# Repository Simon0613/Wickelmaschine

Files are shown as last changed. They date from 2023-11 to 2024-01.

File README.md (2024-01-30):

# Wickelmaschine

### Die Entwicklung und Konstruktion, sowie die Herstellung des Prototyps erfolgte im Rahnen einer Masterarbeit an der Hochschule Osnabrück.

Mit dieser Wickelmaschine können faserverstärkte Rohre z.B. (CFK o. GFK) hergestellt werden. Die Abmessungen der Rohre können nach individuellen Wünschen gestaltet werden und können u.a. für Sport und Campingequipment verwendet werden. Die Maschine arbeitet nach dem Tapelege- oder Tapewickelverfahren, bei dem unidirektional verstärkte Kunststofftapes um den Kern gewickelt und durch eine Wärmequelle mit den unteren Schichten verbunden werden.

Wickelmaschine

Die Wickelmaschine kann mit einfachen Fertigungsverfahren hergestellt werden. Der größte Teil der Bauteile kann mit einem FDM-3D-Drucker angefertigt werden. Weiterhin werden Normteile wie Schrauben, Lager, Einschmelzmuttern und Federn verwendet. Für den Antrieb der Achsen werden Komponenten verwendet die sich in vielen 3D-Druckern wiederfinden: Schrittmotoren, GT2- Riemen und Riemenscheiben, Arduino Uno, CNC-Shield usw.  Der Rest besteht aus Halbzeugen wie Rohren und Flachprofile, die zugesägt, gebohrt und ein wenig gefeilt werden müssen. 

Prototyp

Die Dimensionen der Rohre können nach persönlichen Anforderungen gestalltet werden. Die Maschine kann Rohre mit einen Durchmesser von 15-55 mm herstellen. Die Länge der Rohre ist beliebig einstellbar, nur die Wickelmaschine muss im vorhinein auf die gewünschten Rohrlängen passend angefertigt sein.

3RohreUnterschiedliche Teilung
Nahaufnahme
Überblick Rohre

LizenzOSH

# Montageanleitung

### Folgendes Werkzeug wird für den Bau der Anlage benötigt:

- Bohrmaschine
- Werkzeug zum Anzeichnen der Bohrungen
- Flachfeile
- 3,3 mm Bohrer
- 4,5 mm Bohrer
- M4 Gewindeschneider
- Kegelsenker
- Stirnsenker für M4 Zylinderschrauben
- Lötkolben
- Maßband
- Säge
- Reiniger
- Innensechskantschlüsselsatz

### Aufbauanleitung
Nachdem alle Bauteile entsprechend der Stückliste besorgt wurden, kann mit dem Bauteilzuschnitt begonnen werden. Dazu werden die Rohre entsprechend der Zeichnung_Wellenzuschnitt abgelängt. Die Rohre mit der Bezeichnung T005_Führungsrohr und T060_Kern können je nach persönlichem Wunsch auf eine individuelle Länge abgelängt werden. Sollte der Wunsch bestehen eine Anlage für längere Rohre zu bauen. Die Wellen und Achsen können ebenfalls nach der Zeichnung_Wellenzuschnitt abgelängt werden. Es wird empfohlen die Rohr- und Wellenenden zu entgraten, um sie später besser montieren zu können.
Die Bauteile, die gedruckt werden müssen, sind in folgender Tabelle mit der benötigten Stückzahl gekennzeichnet. Zusätzlich können der Tabelle die Druckeinstellungen für die 3D-Druckteile entnommen werden. Einige Bauteile sind mit „Optional“ markiert, die nur gedruckt werden müssen, sobald ein Material oder eine andere Düse verwendet wird.

1. Zusammenbau der Baugruppe B02_Tapeklemme.
2. 2-mal Zusammenbau Baugruppe B03_Führungswagen.
3. Zusammenbau Baugruppe B05_Grundaufbau_links.
4. Die Baugruppen B03_Führungswagen werden auf die beiden Rohre T005_Führungsrohr aufgeschoben.
5. Die Baugruppen B03_Führungswagen werden mit dem Bauteil T022_Grundplatten mit 12 Innensechskantschrauben verschraubt.
6. Die Baugruppe B06_Grundaufbau_rechts montieren. Hierbei werden die zwei Bauteile T02_Tapeklemme nur leicht eingeschraubt.
7. Die Baugruppe B06_Grundaufbau_rechts wird an die Baugruppe B05_Grundaufbau_links montiert. Jetzt können auch die zwei Klemmen T02_Tapeklemme fest angezogen werden.
8. Die Baugruppe B04_Lagerung_links zusammenbauen. Dazu werden die beiden Klemmen T03_Klemme2 leicht an die Rohre T004_Verbindungsrohr geschraubt. Hier sollte der Abstand von 16,4 mm zwischen dem T019_Riemenspannerhalter und T07_Lagerung_links beachtet werden. Ebenfalls muss auf die Position der beiden Baugruppe relativ zu dem Bauteil T01_Standfuß geachtet werden, die Positionen sind in der Zeichnung B01_Wickelanlage eingezeichnet.
9. Bevor die Baugruppe B07_Antrieb_Rotation an die Rohre T004_Verbindungsrohr angebracht wird, müssen erst folgende Bauteile zusammengefügt werden. Die Riemenscheibe N_Riemenscheibe_GT2_60Z_D8 wird zusammen mit dem N_Riemen_320 auf die Welle T013_Antriebswelle aufgeschoben, der benötigte Abstand ist in der Zeichnung B07_Antrieb_Rotation angegeben. Anschließend wird die Welle T013_Antriebswelle zwischen den Bauteilen T011_Lagergehäuse und T012_Lagergehäuse eingeklemmt. Dieser Verbund wird nun an das Bauteil T09_Lagerung_rechts angeschraubt. Anschließend wird der N_Schrittmotor_Nema17 an T010_Motorbefestigung angeschraubt. Die Riemenscheibe N_Riemenscheibe_GT2_20Z_D5 wird erst auf die Schrittmotorwelle geschoben, nachdem die T010_Motorbefestigung in die Führung von der
T09_Lagerungrechts eingeführt worden ist. Die Spannung der T010_Motorbefestigung und das endgültige Anziehen der T018_Riemenklemme erfolgt später. Die Position der Baugruppe B07_Antrieb_Rotation auf den Rohren T004_Verbindungsrohr ist in Zeichnung B01_Wickelanlage angegeben.
10. Die Montage der Baugruppe B08_Verfahreinheit kann bereits vor dem Schritt 4 ausgeführt werden. Innerhalb der Baugruppe B08_Verfahreinheit wird zuerst die Baugruppe B11_Schwenktisch zusammengebaut. Zuerst müssen die N_Rillenkugellager DIN 625 6000 2Z auf die T029_Achse aufgeschoben werden, die Bemaßung ist in der Schnittansicht der Zeichnung B11_Schwenktisch angegeben. Anschließend werden die beiden Lagerhälften T030_Lager und T030_Lager_Gegenstück zusammen mit T029_Achse verschraubt. Das Bauteil T031_Hülse kann auf die T029_Achse gesetzt werden. Die Bauteile N_Riemenscheibe GT2 60Z D10 und T028_Schwenkplatte werden erst in der Baugruppe B08_Verfahreinheit montiert. Dazu wird der N_Riemen_200 auf die Riemenscheibe N_Riemenscheibe GT2 60Z D10 gelegt und mit der T028_Grundplatte verschraubt. Anschließend kann die Madenschraube der N_Riemenscheibe GT2 60Z D10 angezogen werden, nachdem diese auf die T029_Achse geschoben ist. Im Anschluss können die beiden Schrittmotoren nach der Zeichnung B08_Verfahreinheit an die Bauteile T014_Motorbefestigung2 und T032_Motorbefestigung3 angeschraubt werden. Zuletzt müssen diese an die T022_Grundplatte montiert werden.
11. Die Baugruppe B09_Materialspeicher montieren. Die Feder N_Druckfeder DIN2098 1x10x30 kann je nach Wunsch, stärker gespannt werden, indem die N_Stellring 5mm näher Richtung T037_Materialspeicher geschoben werden.
12. Der Heißluftföhn wird zwischen die Bauteile T046_HalterO und T046_HalterU geklemmt. Diese Baugruppe kann auch auf die T028_Schwenkplatte geschraubt werden. Über die Langlöcher kann die horizontale Entfernung zu dem Kern eingestellt werden. Durch Benutzung der Distanzscheiben T058_Distanzstück wird die vertikale Position zum Kern eingestellt.
13. Die Baugruppe B10_Andrückrolle nach vorliegender Zeichnung montieren. Das Bauteil T057_Tapeführung ist in mehreren Ausführungen vorhanden. Diese sind abhängig von der verwendeten Tapebreite und kann dementsprechende gewechselt werden.
14. Die Baugruppe B02_Tapeklemme auf das Bauteil T060_Kern aufschieben. Anschließend den T060_Kern an der Antriebsseite anschrauben und an der gegenüberliegenden Seite mit zwei T042_Zentrierteil fixieren.
15. Der Heißluftföhn sowie die Baugruppe B09_Materialspeicher können jetzt auf der T028_Schwenkplatte montiert werden.
16. Für die Montage der B10_Andrückrolle ist es empfehlenswert, dass Bauteil T033_Federung durch Lösen von vier Schrauben zu demontieren. Die B10_Andrückrolle auf der T028_Schwenkplatte zu montieren. Anschließend dann das Bauteil T033_Federung wieder anschrauben.
17. Der mechanische Teil der Wickelanlage ist jetzt fertig. Nun folgt der elektrische Teil.

## Elektronik und Steuerung

18. Das CNC-Shield auf den Arduino UNO stecken.
19. Die Jumper auf die für die Treiber vorgesehenen Plätze gemäß der Anleitung des CNC-Shields auf 1/8 Schritte stecken.

JumperPositionierung

20. Die A4988 Schrittmotortreiber auf die X-, Y- und Z-Position aufstecken. Hier ist unbedingt auf die richtige Orientierung zu Achten.
21. Danach werden die Schrittmotorkabel an den Motor sowie an das CNC-Shield angeschlossen. Die X-, Y- und Z-Anschlüsse sind auf dem CNC-Shield und auf folgender Abbildung angezeichnet

MotorBezeichnung

22. Den Arduino UNO mit Strom versorgen und das USB-B Kabel an einen Computer anschließen.

# Estlcam
1. Estlcam auf einem Computer installieren.
2. Anschließend können folgende Einstellungen übernommen werden. Unter dem Menü Einstellungen müssen bei CNC-Steuerung, Grundeinstellungen und CNC Programme Einstellungen vorgenommen werden.
3. Grundeinstellungen und CNC Programme 

GrundeinstellungenESTLCAM

4. CNC Steuerung: Die abgebildeten Werte können einfach übernommen werden. Nachdem alle Werte eingetragen sind sollten diese auch gespeichert werden. Danach kann auf die Schaltfläche Steuerung programmieren geklickt werden.
CNC Steuerung

## Programmabfolge eingeben

1. Die Programmierung der Rohrewicklungen erfolgt über die G-Codes, ähnlich zu einer CNC-Steuerung. Hier muss nur etwas umgedacht werden:

Der Winkel der gewickelt werden soll ergibt sich aus der Bewegung in X-Richtung und der Anzahl der Umdrehungen des Kerns

X-Achse: Die X-Achse entspricht der Länge des Rohres. Dementsprechend wird für ein 100 mm  langes Rohr die Eingabe 100 getätigt.

Z-Achse: Die Z-Achse gibt die Anzahl der Drehungen eines Rohrs vor. Der Kern führt eine Umdrehung(360°) bei einer Eingabe von 100 aus.

Y-Achse: Die Y-Achse passt sich an der Wickelwinkel an. Bei einem Winkel von 45° wird die Y-Achse auf den Wert 4,5 eingestellt.
Achtung! Der Wickelwinkel wird immer von dem Kern gemessen! Das bedeutet wird das Tape gerade um den Kern gewickelt beträgt der Wickelwinkel 90°. Bei der Eingabe muss aber 0 eingegeben werden. Ähnlich bei einem Wickelwinkel von 80° Die Eingabe beträgt hier 1 Bei 70°->2, 60°->3, 50°->4, 45°->4,5

Der maximale Wickelwinkel beträgt 45°. Eingaben der Y-Achse die größer 4,5 sind führen zu einer Kollision.

Grundsätzlich gibt es zwei Arten von Wicklungen einmal Kreuzwickeln und Umfangswickeln

Umfangswickeln: Hier wird während einer Schicht das Tape direkt an das nächste gelegt. Somit wird eine Schicht bei einer Verfahrbewegung fertig.
Diese Art eignet sich besonders wenn Rohre benötigt werden die mit einem Druck von Innen stehen. Beispielhaft wie ein Schlauch oder Tank.

Kreuzwickeln: Diese Wicklungsart ist ein wenig aufwändiger, hat aber dafür vielfältigere Einsatzmöglichkeiten. Diese Rohre eignen sich hervorragend für torsionsbelastete Rohre wie beispielweise Antriebswellen.
Hierbei wird eine Schicht erst durch mehrmaliges hin und zurückfahren fertiggestellt. Die Wicklungen werden dabei kreuzweise übereinandergelegt.

Vor Beginn muss überlegt werden wie viele Umwicklungen man auf einer Rohrlänge haben möchte. Dazu wird der Ausßenradius des Kerns benötigt. Anschließend kann mit folgenden Formel der Wickelwinkel ausgerechnet werden:

FormelnWickelwinkel

Als Beispiel wird dies an einem Rohr mit einer Länge von 100 mm gezeigt das nach dem Umfangswickelprinzip gewickelt wird.

Erstellung Programmabfolge

Die Programme können einfach im Text Editor erstellt werden. Bei Fertigstellung des Programms wird der Dateityp von .txt in . nc geändert. Danach kann ESTLCAM das Programm einlesen.

Die Wicklung der Rohre erfolgt in folgender Reihenfolge. Grundsätzlich kann sich an die folgende Vorgehensweise gehalten werden:

grafik
Im ersten Schritt werden vorbereitende Maßnahmen durchgeführt. Dazu gehört den Kern reinigen und das Material auf den B09_Materialspeicher aufzuwickeln. Die Position der Y-Achse wird ausgerichtet, indem T022_Grundplatte und T028_Schwenkplatte parallel zueinander ausgerichtet werden. Die Z-Achse kann auf 0 gesetzt werden. Die X-Achse kann an gewünschter Position auf 0 gesetzt werden, jedoch sollte auf die ausreichende Länge geachtet werden.
Anschließend wird das Material über die T050_Umlenkrolle gelegt und durch die T039_Materialzuführ geführt. Danach wird das Material unter die Andrückrolle geführt und min. zweimal um den Kern gewickelt. Das Ende wird durch die B02_Tapeklemme festgeklemmt. Jetzt kann das Programm in Estlcam hochgela-den werden. Zuerst wird der Heißluftföhn eingeschaltet und für ca. 30 s angelas-sen. Nachdem die Vorheizzeit vorüber ist, wird das Programm gestartet. Wenn das Programm durchgelaufen ist, kann der Heißluftföhn ausgeschaltet werden und das Material wird direkt am Kern durchtrennt. Sobald der Kern abgekühlt ist, kann die-ser aus der Anlage entfernt werden. Danach kann das fertige Rohr vom Kern ab-gezogen werden.

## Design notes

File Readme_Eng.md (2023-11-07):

# Windingmachine

### This winding machine was developed and built as part of a master's thesis at the University of Applied Sciences in Osnabrück, Germany.  

This winding machine can be used to produce fibre reinforced tubes. The dimensions of the tubes can be customised for use in sports and camping equipment, for example. The machine uses the tape laying or tape winding process, where unidirectional reinforced plastic tapes are wound around the core and bonded to the lower layers using a heat source.

Wickelmaschine

The winding machine can be produced using simple manufacturing methods. Most of the components can be produced using an FDM 3D printer. Standard parts such as bolts, screws, bearings, heat sink inserts and springs are used. The power unit includes stepper motors and other parts you can find in 3D printers, such as GT2 pulleys and belts, the Arduino uno and a CNC shield. The other components are semi-finished materials, such as tubes and profiles, which need to be machined with drills, saws and files.

Prototyp
The dimensions of the tubes can be customised. The machine is capable of producing tubes ranging from 15-55 mm ( 0.6 - 2.1 inches). The lengths of the tubes can be adjusted as required, but the winding machine must be built long enough.
3RohreUnterschiedliche Teilung
Nahaufnahme
Überblick Rohre

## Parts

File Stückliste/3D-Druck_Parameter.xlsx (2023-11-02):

 |  |  |  | Material
Name | Fülldichte | Wandstärke | Anzahl | PLA/PETG | ABS/ASA | PA
T001_Standfuß | 20% | 5 | 2 | xxx | xxx | x
T001_Standfuß_gsp | 20% | 5 | 2 | xxx | xxx | x
T002_Klemme1 | 20% | 5 | 4 | xxx | xxx | x
T003_Klemme2 | 20% | 5 | 7 | xxx | xxx | x
T006_Führungswagen | 20% | 5 | 2 | xxx | xxx | x
T007_Lagerung_links | 20% | 5 | 1 | xxx | xxx | x
T008_Lagerungshalter | 20% | 5 | 1 | xxx | xxx | x
T009_Lagerung_rechts | 20% | 5 | 1 | xxx | xxx | x
T010_Motorbefestigung | 20% | 5 | 1 | xxx | xxx | x
T011_Lagergehäuse | 20% | 4 | 1 | xxx | xxx | x
T012_Lagergehäuse | 20% | 4 | 1 | xxx | xxx | x
T014_Motorbefestigung2 | 20% | 4 | 1 | xxx | xxx | x
T015_Halter | 20% | 4 | 1 | xxx | xxx | x
T016_Klemme Riemen | 20% | 3 | 1 | xxx | xxx | x
T017_Riemenklemme | 20% | 3 | 1 | xxx | xxx | x
T018_Riemenspanner_H | 20% | 4 | 1 | xxx | xxx | x
T019_RiemenspannerHalter | 20% | 4 | 1 | xxx | xxx | x
T020_RiemenspannerHalter2 | 20% | 4 | 1 | xxx | xxx | x
T023_Materialhalter | 15% | 3 | 1 | xxx | xxx | x
T024_Klemmhebel | 20% | 3 | 1 | - | xx | xxx
T025_Tapeklemme | 20% | 4 | 1 | - | xxx | xxx
T026_Spule | 20% | 4 | 1 | xxx | xxx | x
T030_Lager | 40% | 5 | 1 | xx | xxx | xx
T030_Lager_Gegenstück | 40% | 5 | 1 | xx | xxx | xx
T031_Hülse | 20% | 4 | 1 | xx | xxx | xx
T032_Motorbefestigung3 | 20% | 4 | 1 | xxx | xxx | x
T033_Federung | 20% | 4 | 1 | x | xxx | xxx
T034_Federhalter | 20% | 5 | 1 | x | xxx | xxx
T035_Schieber | 30% | 5 | 1 | - | xx | xxx
T037_Materialspeicher | 20% | 3 | 1 | xxx | xxx | x
T037_Materialspeicher_Gegenstück | 20% | 3 | 1 | xxx | xxx | x
T039_Materialzufuhr | 20% | 4 | 1 | - | xx | xxx
T039_Materialzufuhr_Gegenstück | 20% | 4 | 1 | - | xx | xxx
T041_Rohraufnahme_links_21mm | 30% | 4 | 1 | - | xxx | xxx
T042_Zentrierteil | 20% | 4 | 2 | x | xxx | xx
T043_Rohraufnahme_rechts | 30% | 4 | 1 | x | xxx | xxx
T044_Riemenspannung | 20% | 3 | 1 | xxx | xxx | x
T046_HLHalterO | 20% | 4 | 1 | xxx | xxx | x
T046_HLHalterU | 20% | 4 | 1 | xxx | xxx | x
T047_Anschlag45° | 15% | 3 | 1 | xx | xxx | xx
T048_Sensorhalter_X | 15% | 4 | 1 | xxx | xxx | x
T048_Sensorhalter_X_Gegenstück | 15% | 4 | 1 | xxx | xxx | x
T049_Spurhalter | 20% | 4 | 1 | xx | xxx | x
T050_Umlenkrolle | 20% | 4 | 1 | xxx | xxx | x
T051_Halter_Umlenkung1 | 20% | 3 | 1 | xxx | xxx | x
T051_Halter_Umlenkung1gsp | 20% | 3 | 1 | xxx | xxx | x
T053_HalterArduino | 20% | 4 | 1 | xxx | xxx | x
T054_KlemmeArduino | 20% | 4 | 1 | xxx | xxx | x
T055_KabelkanalAnschluss | 20% | 4 | 1 | xxx | xxx | x
T056_Abstandshülse | 20% | 4 | 2 | xx | xxx | xx
T057_Tapeführung_3mm | 20% | 3 | 1 | - | xx | xxx
T057_Tapeführung_6mm | 20% | 3 | Optional | - | xx | xxx
T057_Tapeführung_10mm | 20% | 3 | Optional | - | xx | xxx
T058_Distanzstück_5mm | 20% | 3 | Optional | xxx | xx | x
T058_Distanzstück_10mm | 20% | 3 | Optional | xxx | xx | x
T059_Bohrschablone | 10% | 3 | Optional | xxx | xx | x
T061_Bremsklotz | 20% | 3 | Optional | xxx | xxx | x
T062_Lüfterhalter | 30% | 5 | Optional | xxx | xxx | x
T063_Kabelführung | 20% | 3 | Optional | xxx | xxx | x
 |  |  |  | - | Materialversagen
 |  |  |  | x | nicht ideales Material
 |  |  |  | xx | Funktioniert
 |  |  |  | xxx | Optimales Material

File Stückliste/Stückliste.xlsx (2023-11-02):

Nr. | Bauteilname | Anzahl | Bauteilart
1 | N_ANDRÜCKROLLE | 1 | Kaufteil
2 | N_ArduinoUNO | 1 | Kaufteil
3 | N_CNC_Shield | 1 | Kaufteil
4 | N_DRUCKFEDER DIN 2098 0,5X6X10 | 1 | Kaufteil
5 | N_DRUCKFEDER DIN 2098 1X10X30 | 3 | Kaufteil
6 | N_DUMMY_KABELKANAL | 1 | Kaufteil
7 | N_EINSCHMELZMUTTER M3 KURZ | 4 | Kaufteil
8 | N_EINSCHMELZMUTTER M4 | 145 | Kaufteil
9 | N_EINSCHMELZMUTTER M5 | 4 | Kaufteil
10 | N_Endschalter_3Pin | 2 | Kaufteil
11 | N_Hitzeschutzfolie | 1 | Kaufteil
12 | N_LINEARLAGER | 1 | Kaufteil
13 | N_Netzteil_12V_5A | 1 | Kaufteil
14 | N_RIEMEN_GT2_6MM_L1000 | 1 | Kaufteil
15 | N_RIEMEN_GT2_6MM_L200_GESCHLOSSEN | 1 | Kaufteil
16 | N_RIEMEN_GT2_6MM_L320_GESCHLOSSEN | 1 | Kaufteil
17 | N_RIEMENSCHEIBE GT2 20Z D5 | 3 | Kaufteil
18 | N_RIEMENSCHEIBE GT2 60Z D10 | 1 | Kaufteil
19 | N_RIEMENSCHEIBE GT2 60Z D8 | 1 | Kaufteil
20 | N_RILLENKUGELLAGER DIN 625 608 | 3 | Kaufteil
21 | N_RILLENKUGELLAGER DIN 625-625-2Z | 14 | Kaufteil
22 | N_RILLENKUGELLAHER DIN 625 6000-2Z | 2 | Kaufteil
23 | N_SCHEIBE ISO 7092-4 | 10 | Kaufteil
24 | N_SCHEIBE ISO 8738-1 | 28 | Kaufteil
25 | N_SCHRITTMOTOR_NEMA17 | 3 | Kaufteil
26 | N_Schrittmototkabel_0,5m_4auf6Pin_HX2.54 | 1 | Kaufteil
27 | N_Schrittmototkabel_1,5m_4auf6Pin_HX2.54 | 2 | Kaufteil
28 | N_SECHSKANTMUTTER ISO 4032-M5 | 12 | Kaufteil
29 | N_STEINELHEIßLUFTFÖHN_HG2220E | 1 | Kaufteil
30 | N_STELLRING 5MM | 2 | Kaufteil
31 | N_USB-Bkabel | 1 | Kaufteil
32 | N_Flanschkugellager F695 2RS 5x13x4 | 4 | Kaufteil
33 | N_WELLENKUPPLUNGSFLANSCH_8MM | 1 | Kaufteil
34 | N_ZYLINDERSCHRAUBE ISO 4762-M3X12 | 8 | Kaufteil
35 | N_ZYLINDERSCHRAUBE ISO 4762-M3X25 | 6 | Kaufteil
36 | N_ZYLINDERSCHRAUBE ISO 4762-M3X8 | 9 | Kaufteil
37 | N_ZYLINDERSCHRAUBE ISO 4762-M4X12 | 75 | Kaufteil
38 | N_ZYLINDERSCHRAUBE ISO 4762-M4X20 | 101 | Kaufteil
39 | N_ZYLINDERSCHRAUBE ISO 4762-M5X20 | 11 | Kaufteil
40 | N_ZYLINDERSCHRAUBE ISO 4762-M5X30 | 12 | Kaufteil
41 | T001_STANDFUß | 2 | Druckteil
42 | T001_STANDFUß_GSP | 2 | Druckteil
43 | T002_KLEMME1 | 4 | Druckteil
44 | T003_KLEMME2 | 7 | Druckteil
45 | T004_VERBINDUNGSROHR | 4 | Stahl
46 | T005_FÜHRUNGSROHR | 2 | Stahl
47 | T006_FÜHRUNGSWAGEN | 2 | Druckteil
48 | T007_LAGERUNG_LINKS | 1 | Druckteil
49 | T008_LAGERUNGSHALTER | 1 | Druckteil
50 | T009_LAGERUNG_RECHTS | 1 | Druckteil
51 | T010_MOTORBEFESTIGUNG | 1 | Druckteil
52 | T011_LAGERGEHÄUSE | 1 | Druckteil
53 | T012_LAGERGEHÄUSE | 1 | Druckteil
54 | T013_ANTRIEBSWELLE | 1 | Stahl
55 | T014_MOTORBEFESTIGUNG2 | 1 | Druckteil
56 | T015_HALTER | 1 | Druckteil
57 | T016_KLEMME RIEMEN | 1 | Druckteil
58 | T017_RIEMENKLEMME | 2 | Druckteil
59 | T018_RIEMENSPANNER_H | 1 | Druckteil
60 | T019_RIEMENSPANNERHALTER | 1 | Druckteil
61 | T020_RIEMENSPANNERHALTER2 | 1 | Druckteil
62 | T021_ACHSE | 1 | Stahl
63 | T022_GRUNDPLATTE | 1 | Aluminium
64 | T023_MATERIALHALTER | 1 | Druckteil
65 | T024_KLEMMHEBEL | 1 | Druckteil
66 | T025_TAPEKLEMME | 1 | Druckteil
67 | T026_SPULE | 1 | Druckteil
68 | T028_SCHWENKPLATTE | 1 | Aluminium
69 | T029_ACHSE | 1 | Stahl
70 | T030_LAGER | 1 | Druckteil
71 | T030_LAGER_GEGENSTÜCK | 1 | Druckteil
72 | T031_HÜLSE | 1 | Druckteil
73 | T032_MOTORBEFESTIGUNG3 | 1 | Druckteil
74 | T033_FEDERUNG | 1 | Druckteil
75 | T034_FEDERHALTER | 1 | Druckteil
76 | T035_SCHIEBER | 1 | Druckteil
77 | T036_ACHSE | 1 | Stahl
78 | T037_MATERIALSPEICHER | 1 | Druckteil
79 | T037_MATERIALSPEICHER_GEGENSTÜCK | 1 | Druckteil
80 | T038_FLACHEISEN | 2 | Aluminium
81 | T039_MATERIALZUFUHR | 1 | Druckteil
82 | T039_MATERIALZUFUHR_GEGENSTÜCK | 1 | Druckteil
83 | T040_ACHSE_LINKS | 1 | Stahl
84 | T041_ROHRAUFNAHME_LINKS_21MM | 1 | Druckteil
85 | T042_ZENTRIERTEIL | 1 | Druckteil
86 | T043_ROHRAUFNAHME_RECHTS | 1 | Druckteil
87 | T044_RIEMENSPANNUNG | 1 | Druckteil
88 | T045_ACHSE_ANDRÜCKROLLE | 1 | Stahl
89 | T046_HLHALTERO | 1 | Druckteil
90 | T046_HLHALTERU | 1 | Druckteil
91 | T047_ANSCHLAG45° | 1 | Druckteil
92 | T048_SENSORHALTER_X | 1 | Druckteil
93 | T048_SENSORHALTER_X_GEGENSTÜCK | 1 | Druckteil
94 | T049_SPURHALTER | 1 | Druckteil
95 | T050_UMLENKROLLE | 1 | Druckteil
96 | T051_HALTER_UMLENKUNG1 | 1 | Druckteil
97 | T051_HALTER_UMLENKUNG1GSP | 1 | Druckteil
98 | T052_ACHSE_UMLENKUNG | 1 | Stahl
99 | T053_HALTERARDUINO | 1 | Druckteil
100 | T054_KLEMMEARDUINO | 1 | Druckteil
101 | T055_KABELKANALANSCHLUSS | 1 | Druckteil
102 | T056_ABSTANDSHÜLSE | 2 | Druckteil
103 | T057_TAPEFÜHRUNG_3MM | 1 | Druckteil
104 | T060_KERN_25MM | 1 | Stahl
105 | T061_Bremsklotz | 1 | Druckteil
106 | T062_Lüfterhalter | 1 | Druckteil
107 | T063_Kabelführung | 1 | Druckteil

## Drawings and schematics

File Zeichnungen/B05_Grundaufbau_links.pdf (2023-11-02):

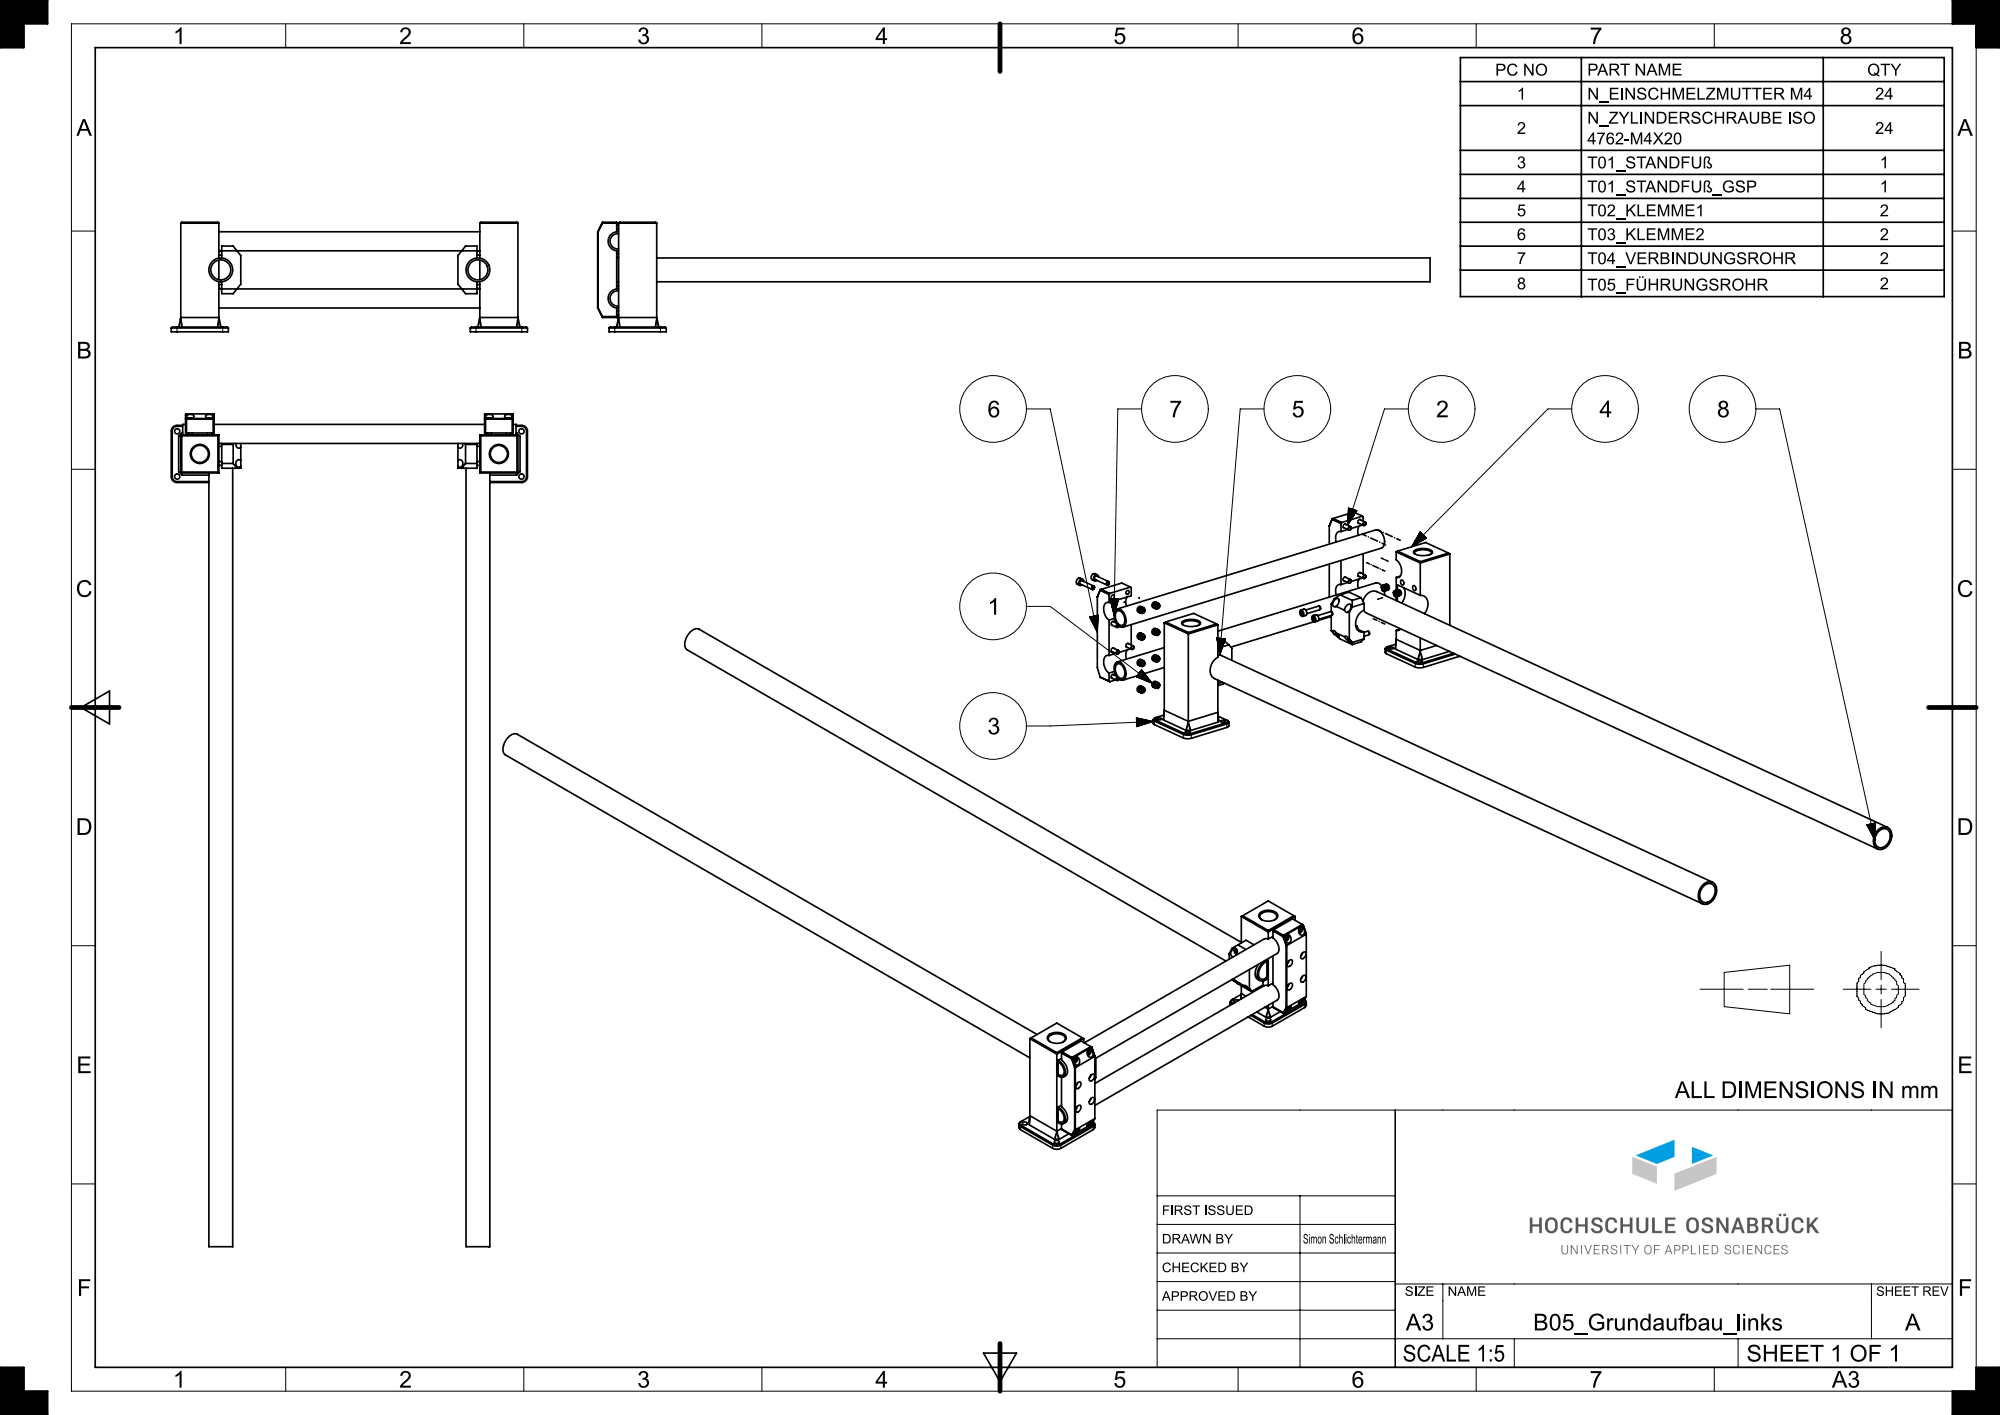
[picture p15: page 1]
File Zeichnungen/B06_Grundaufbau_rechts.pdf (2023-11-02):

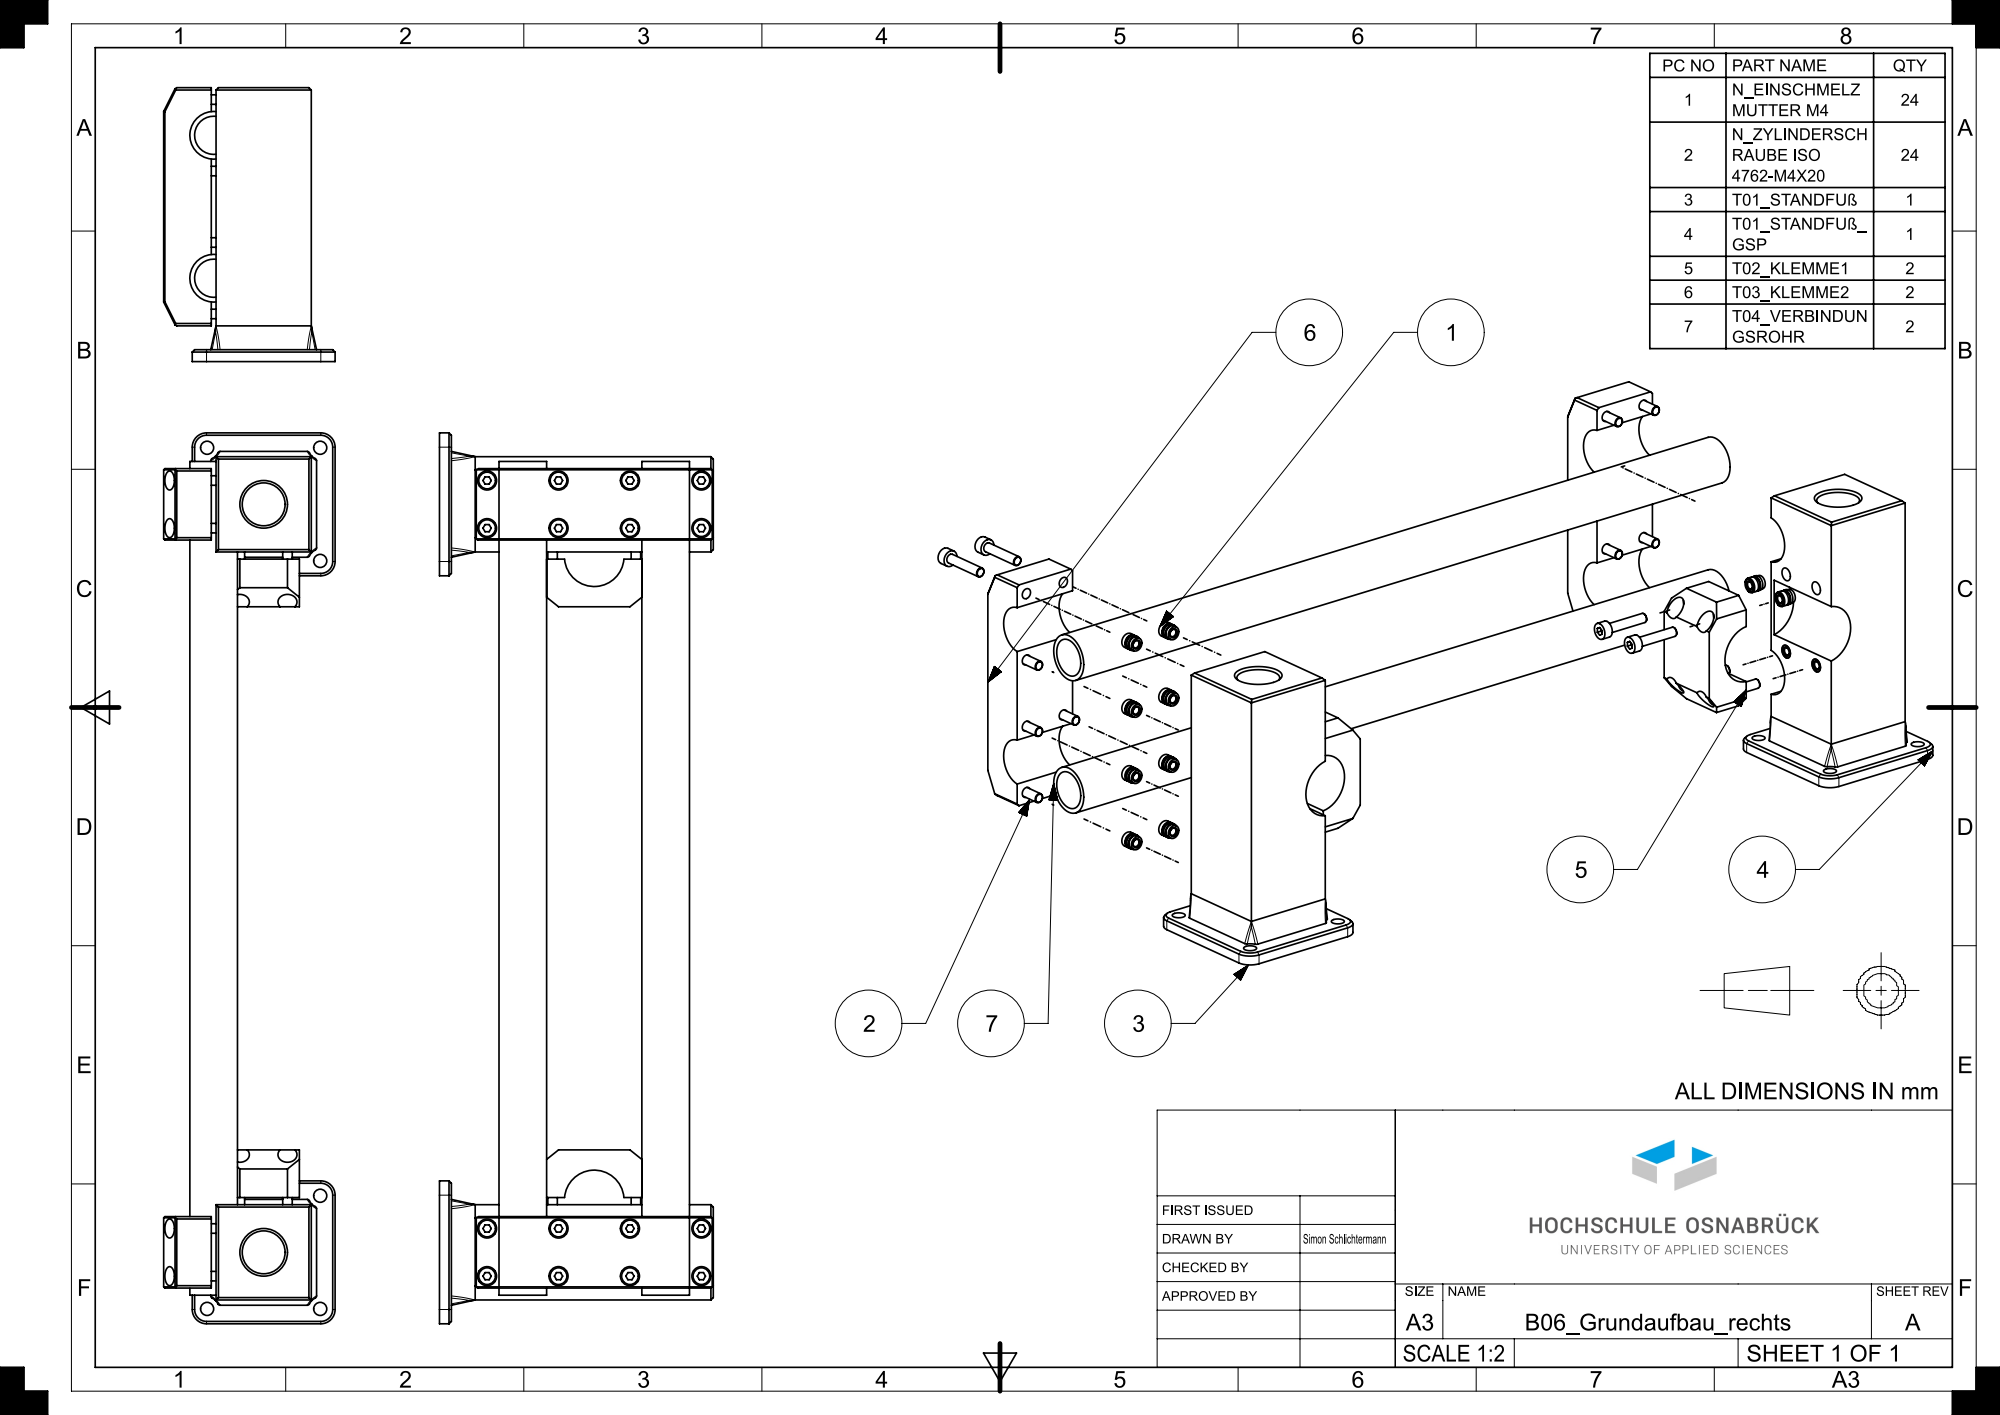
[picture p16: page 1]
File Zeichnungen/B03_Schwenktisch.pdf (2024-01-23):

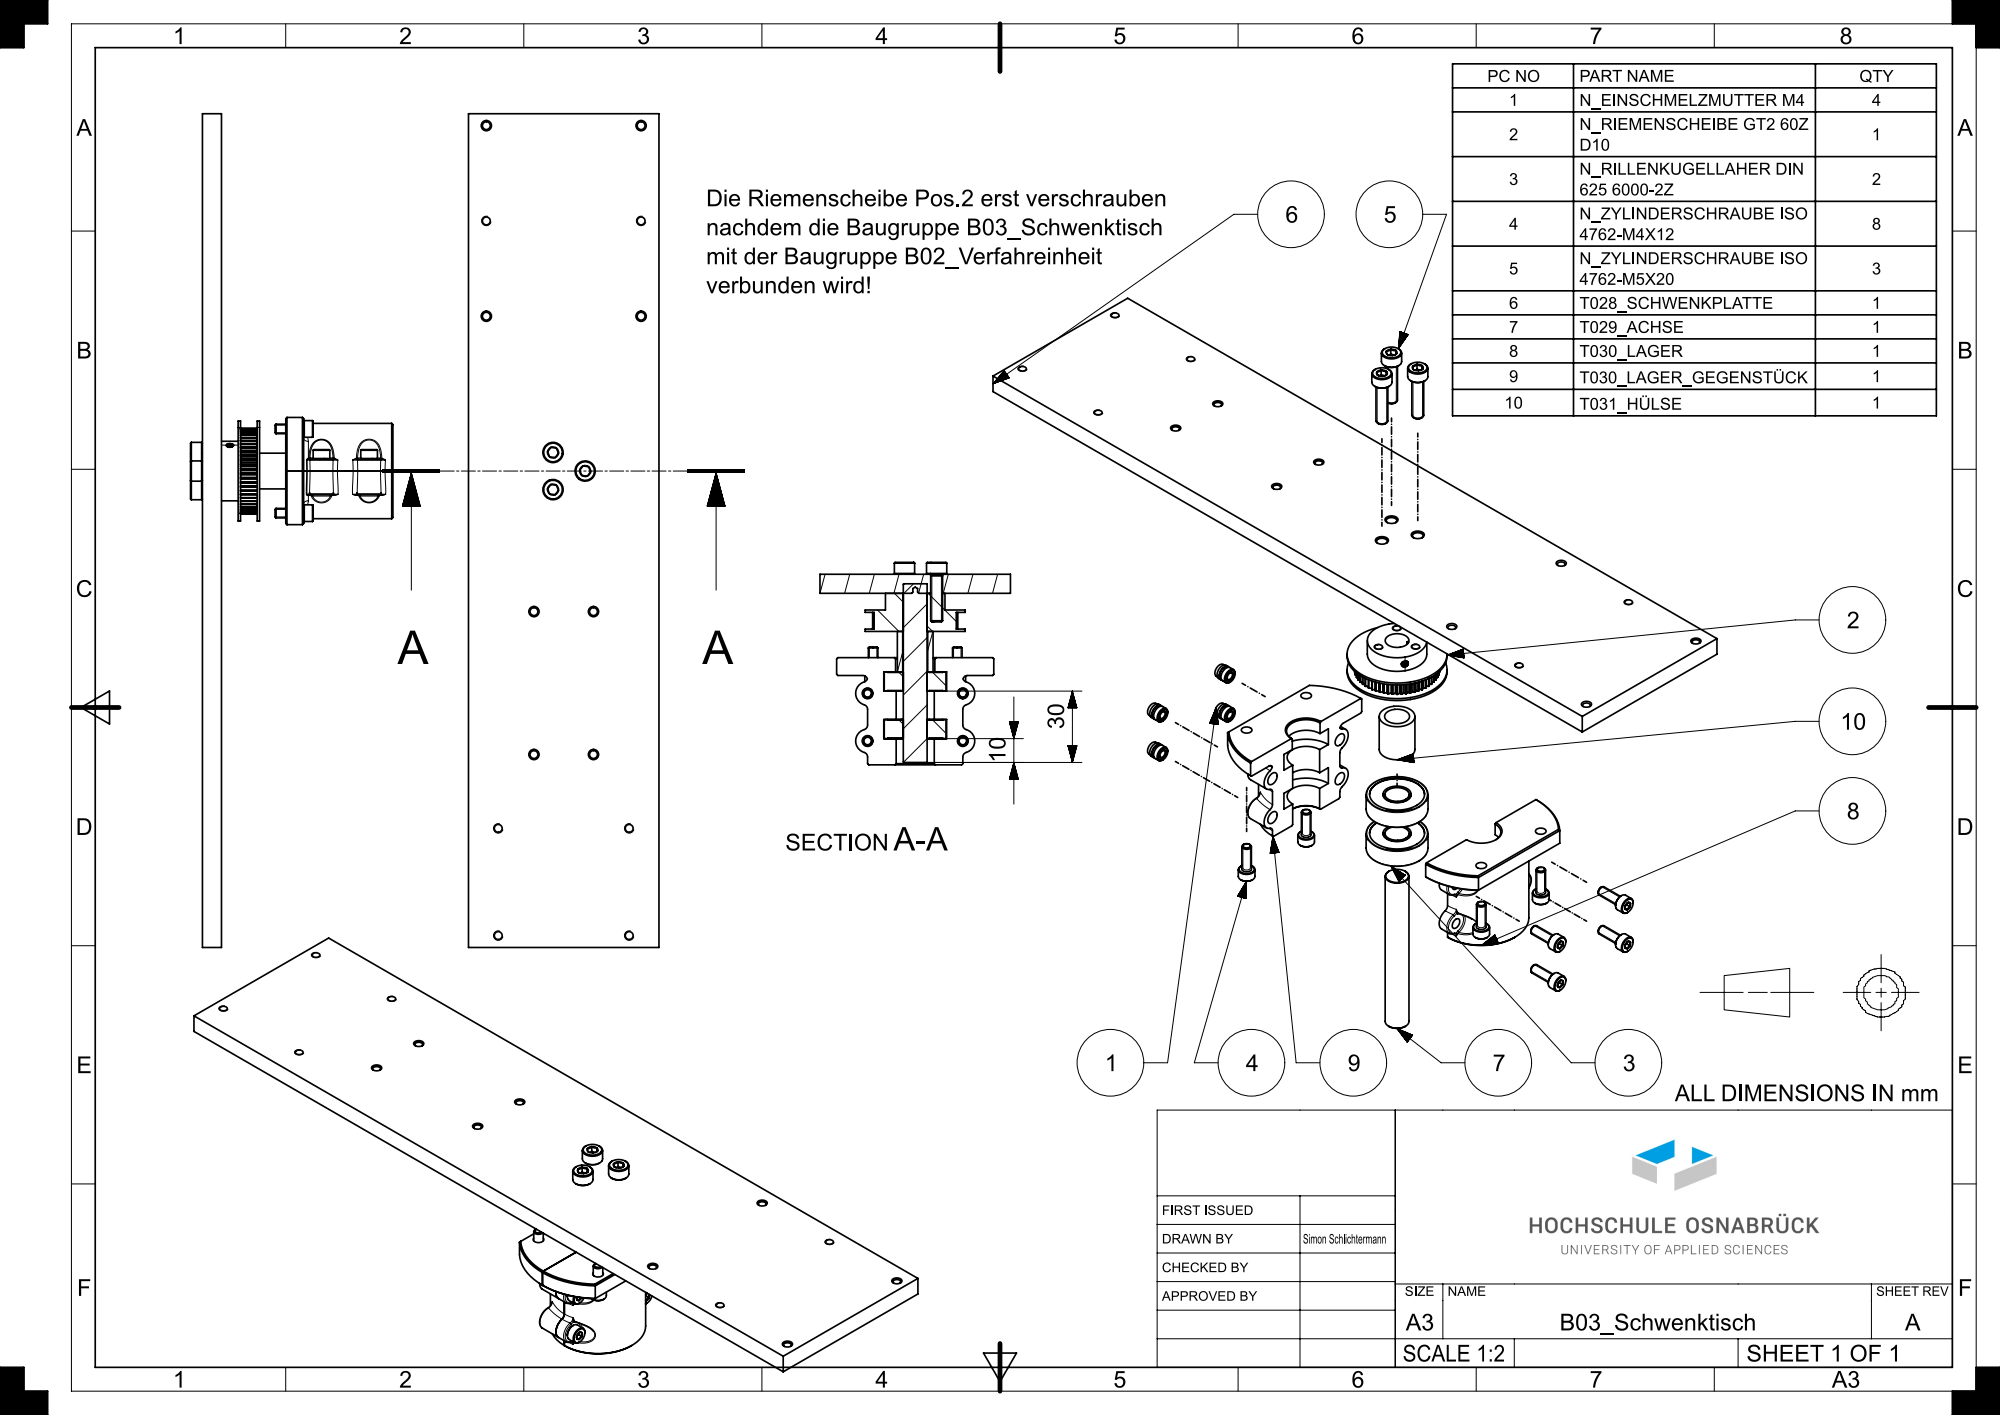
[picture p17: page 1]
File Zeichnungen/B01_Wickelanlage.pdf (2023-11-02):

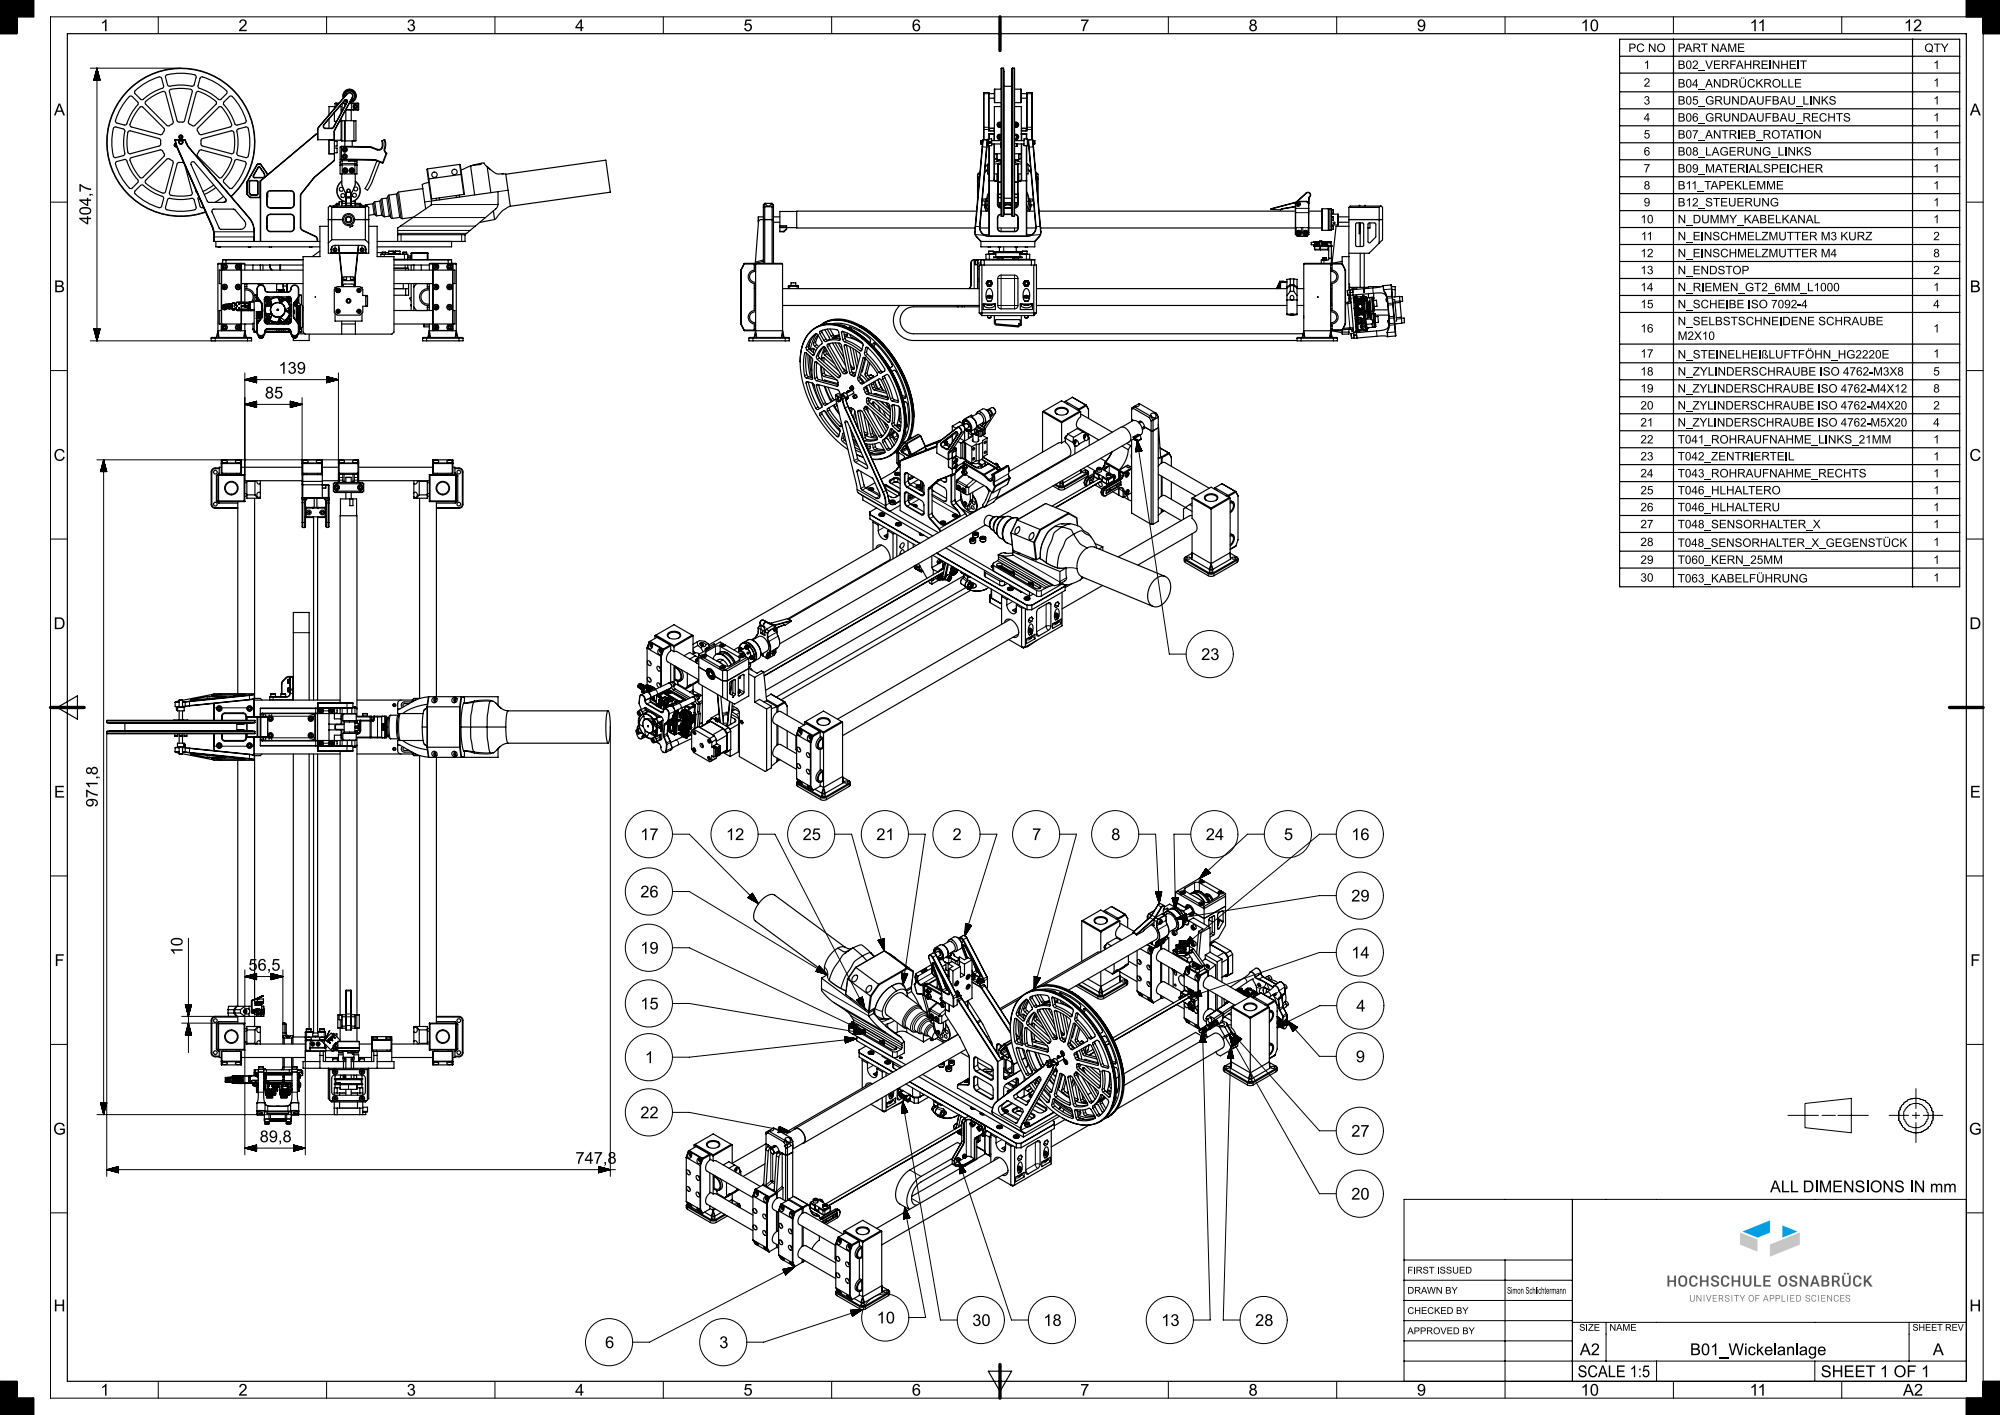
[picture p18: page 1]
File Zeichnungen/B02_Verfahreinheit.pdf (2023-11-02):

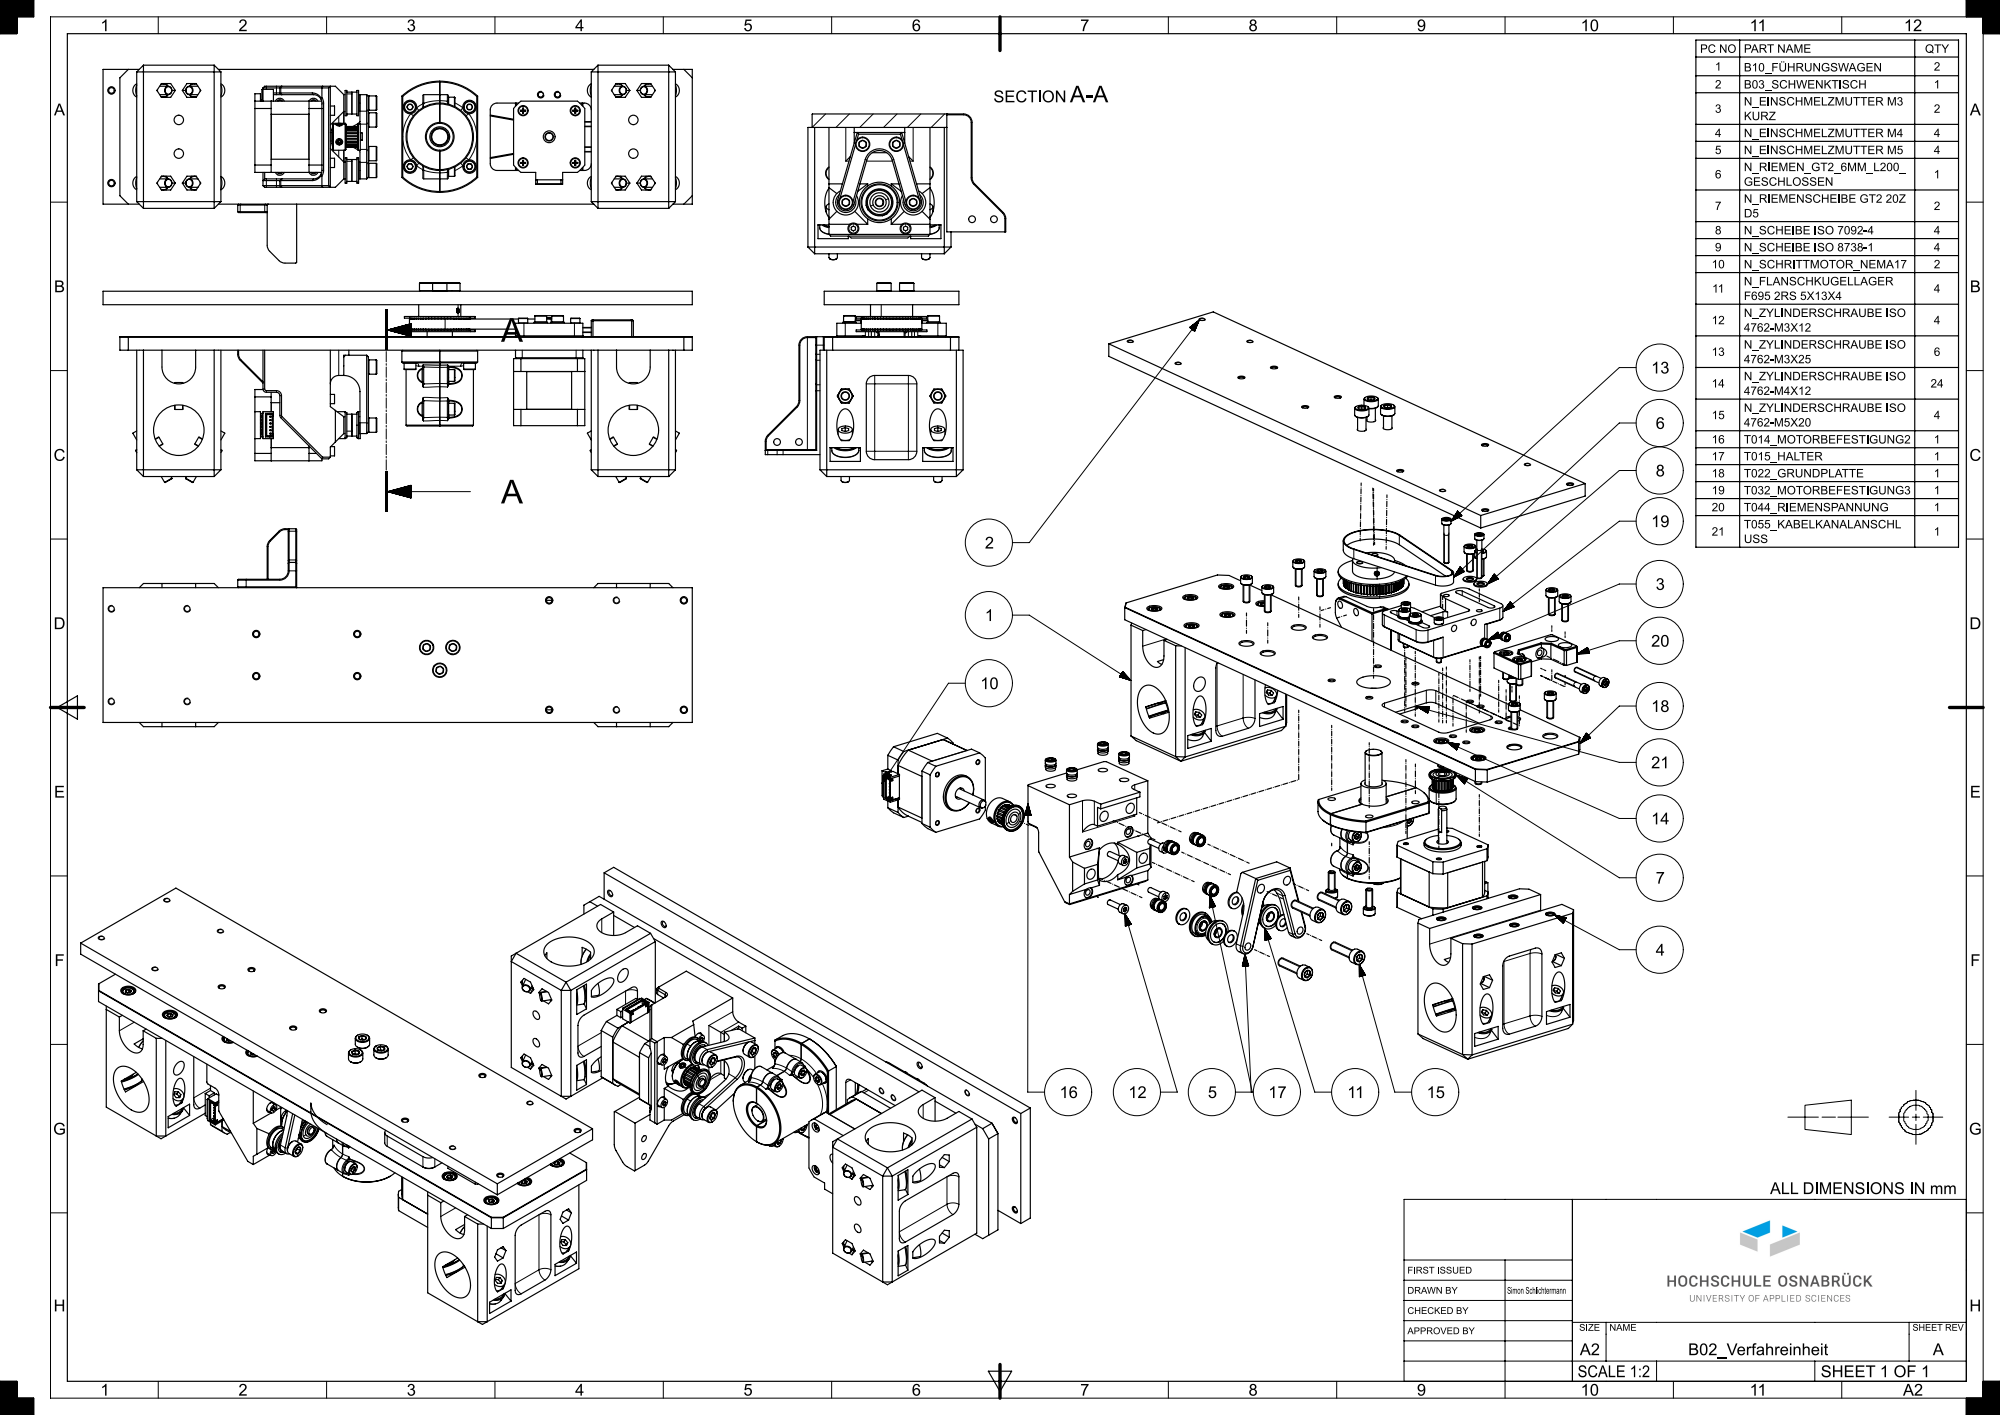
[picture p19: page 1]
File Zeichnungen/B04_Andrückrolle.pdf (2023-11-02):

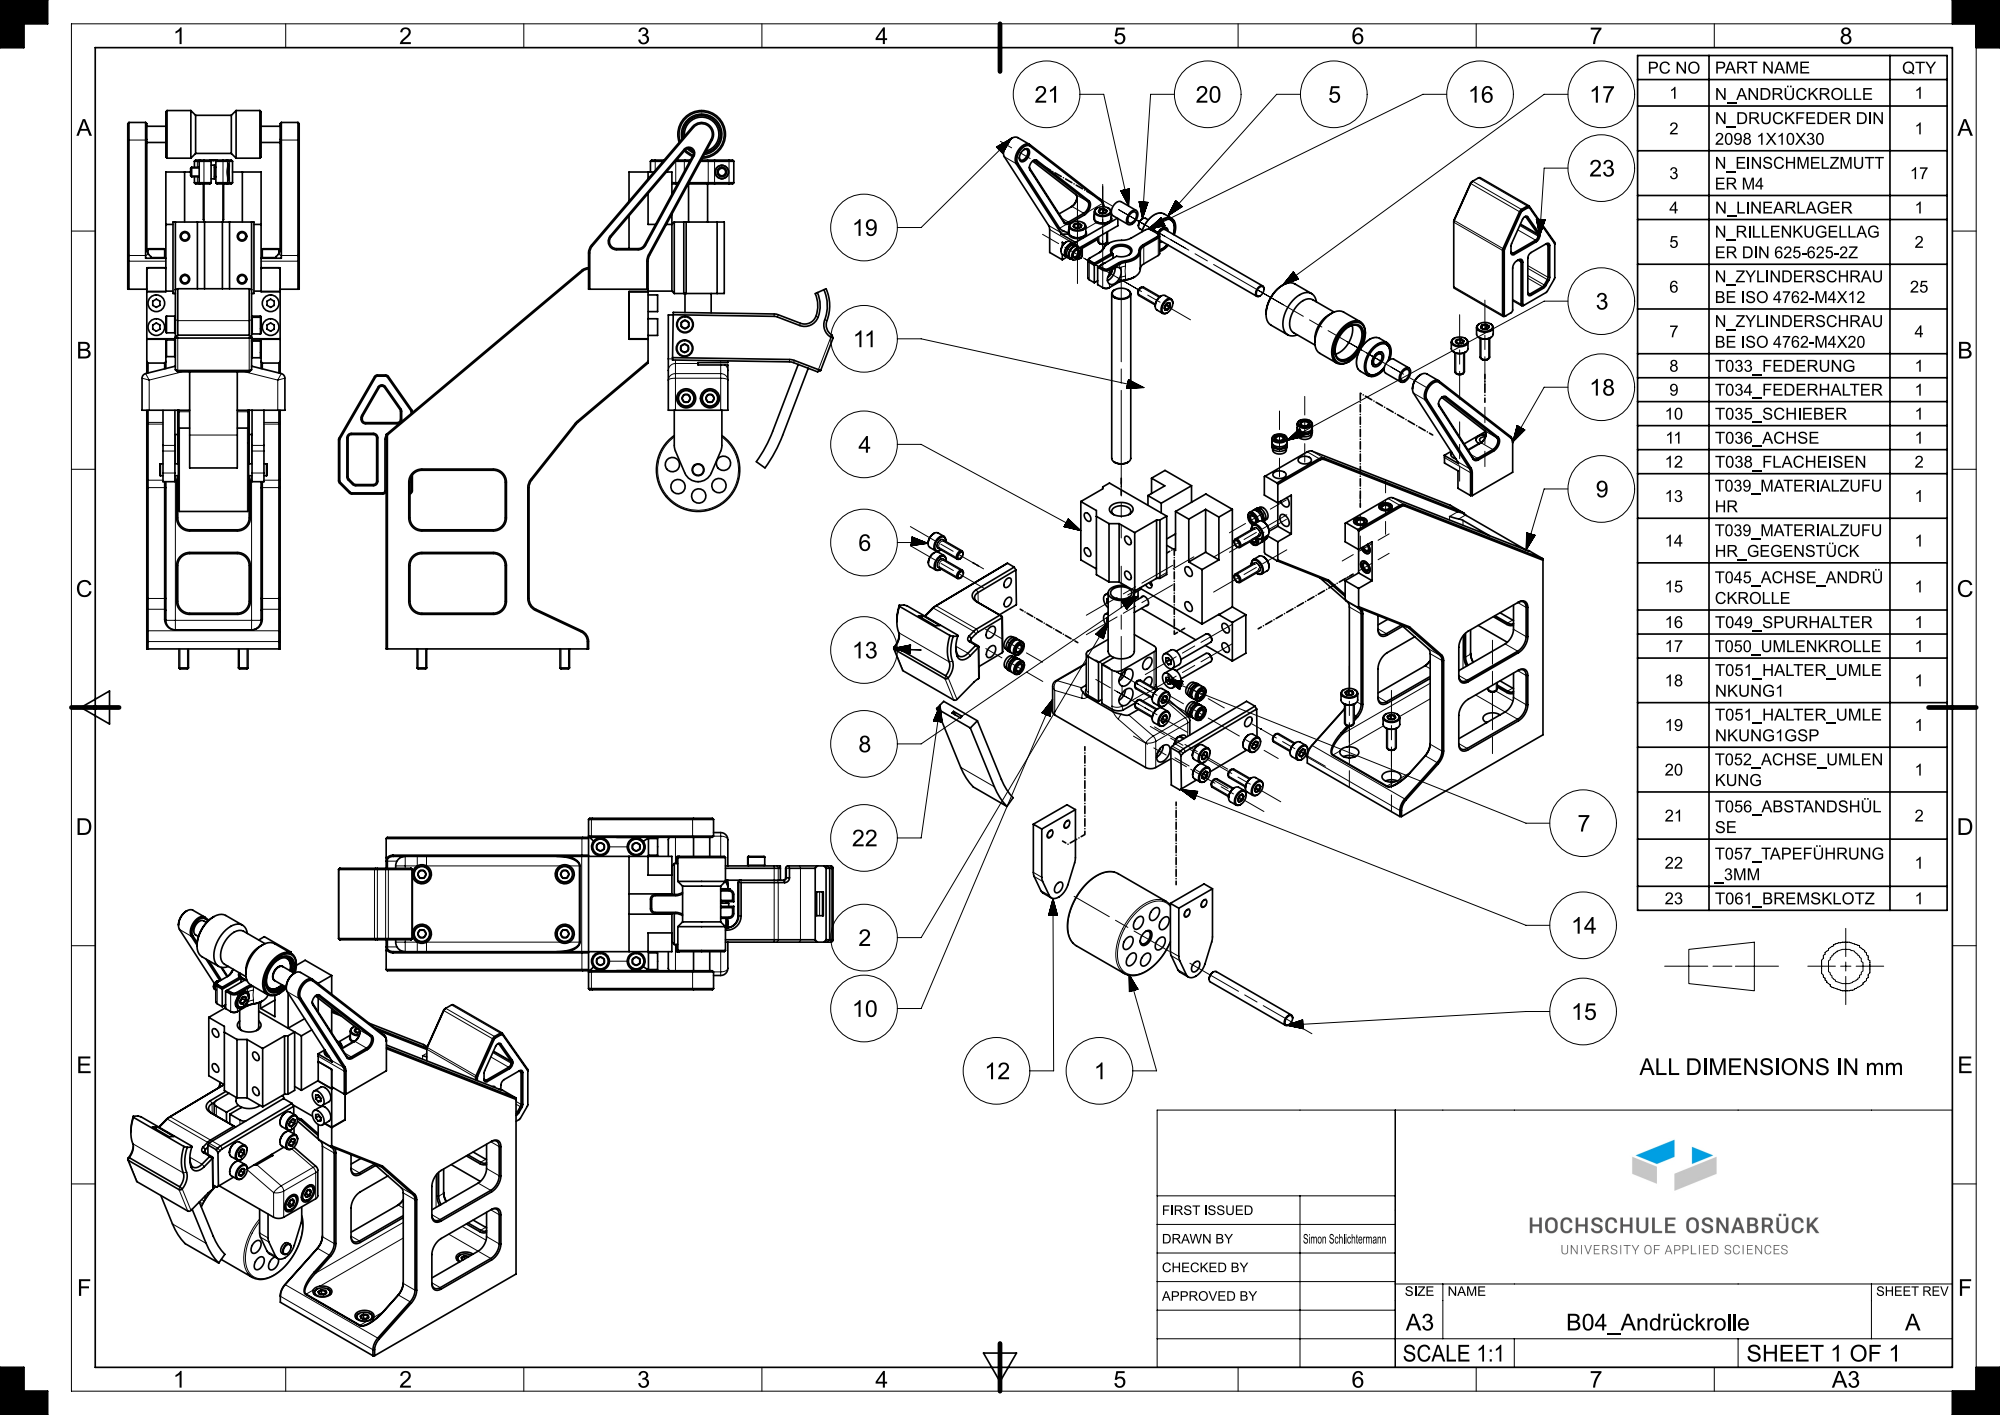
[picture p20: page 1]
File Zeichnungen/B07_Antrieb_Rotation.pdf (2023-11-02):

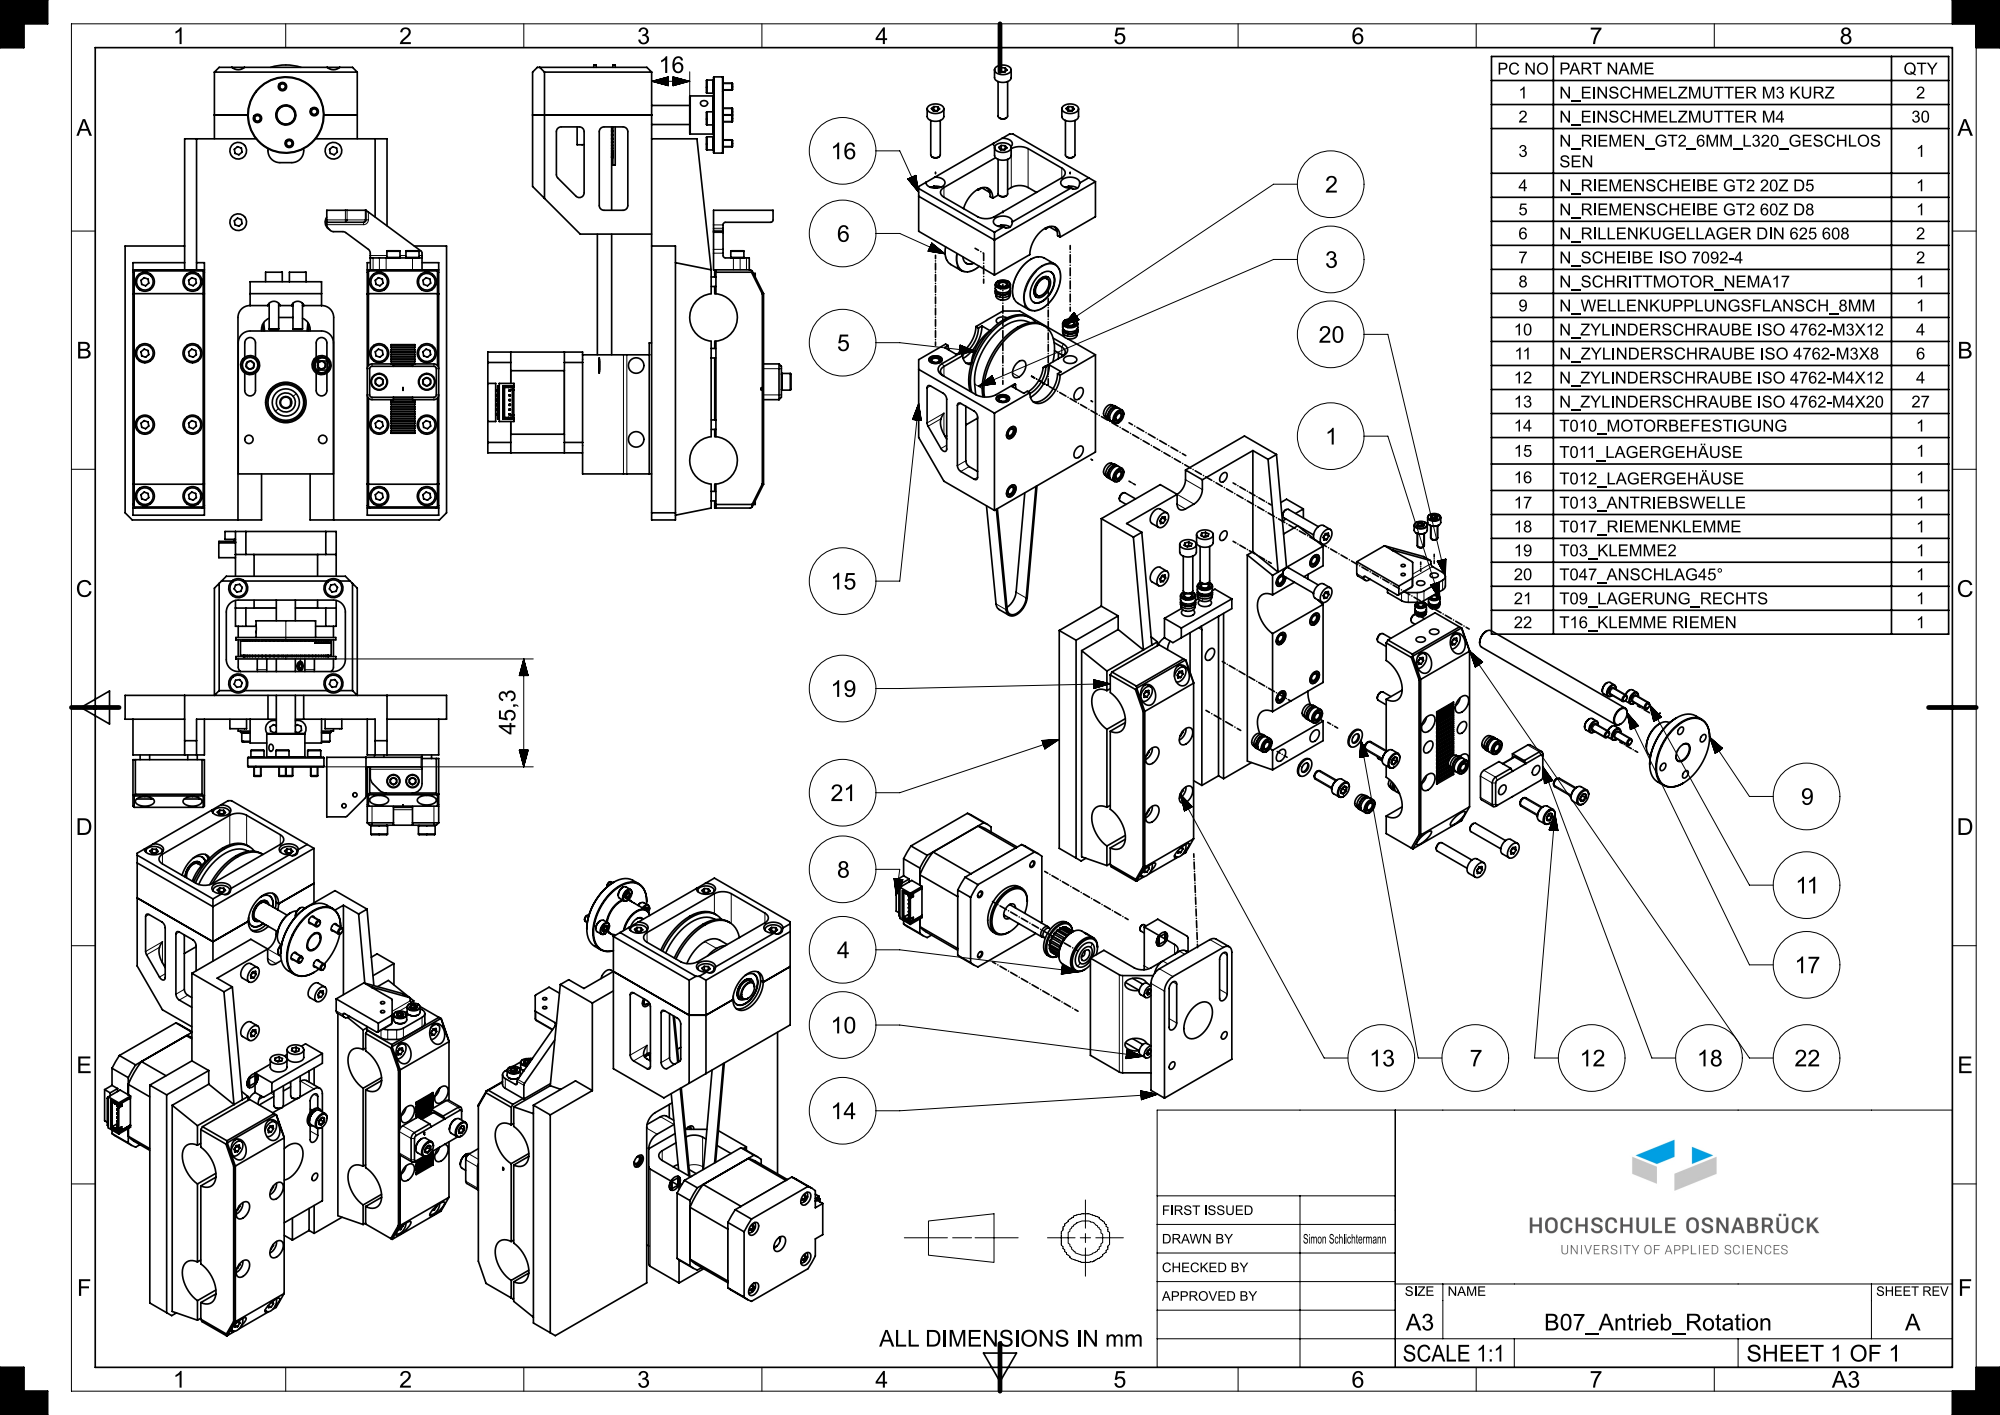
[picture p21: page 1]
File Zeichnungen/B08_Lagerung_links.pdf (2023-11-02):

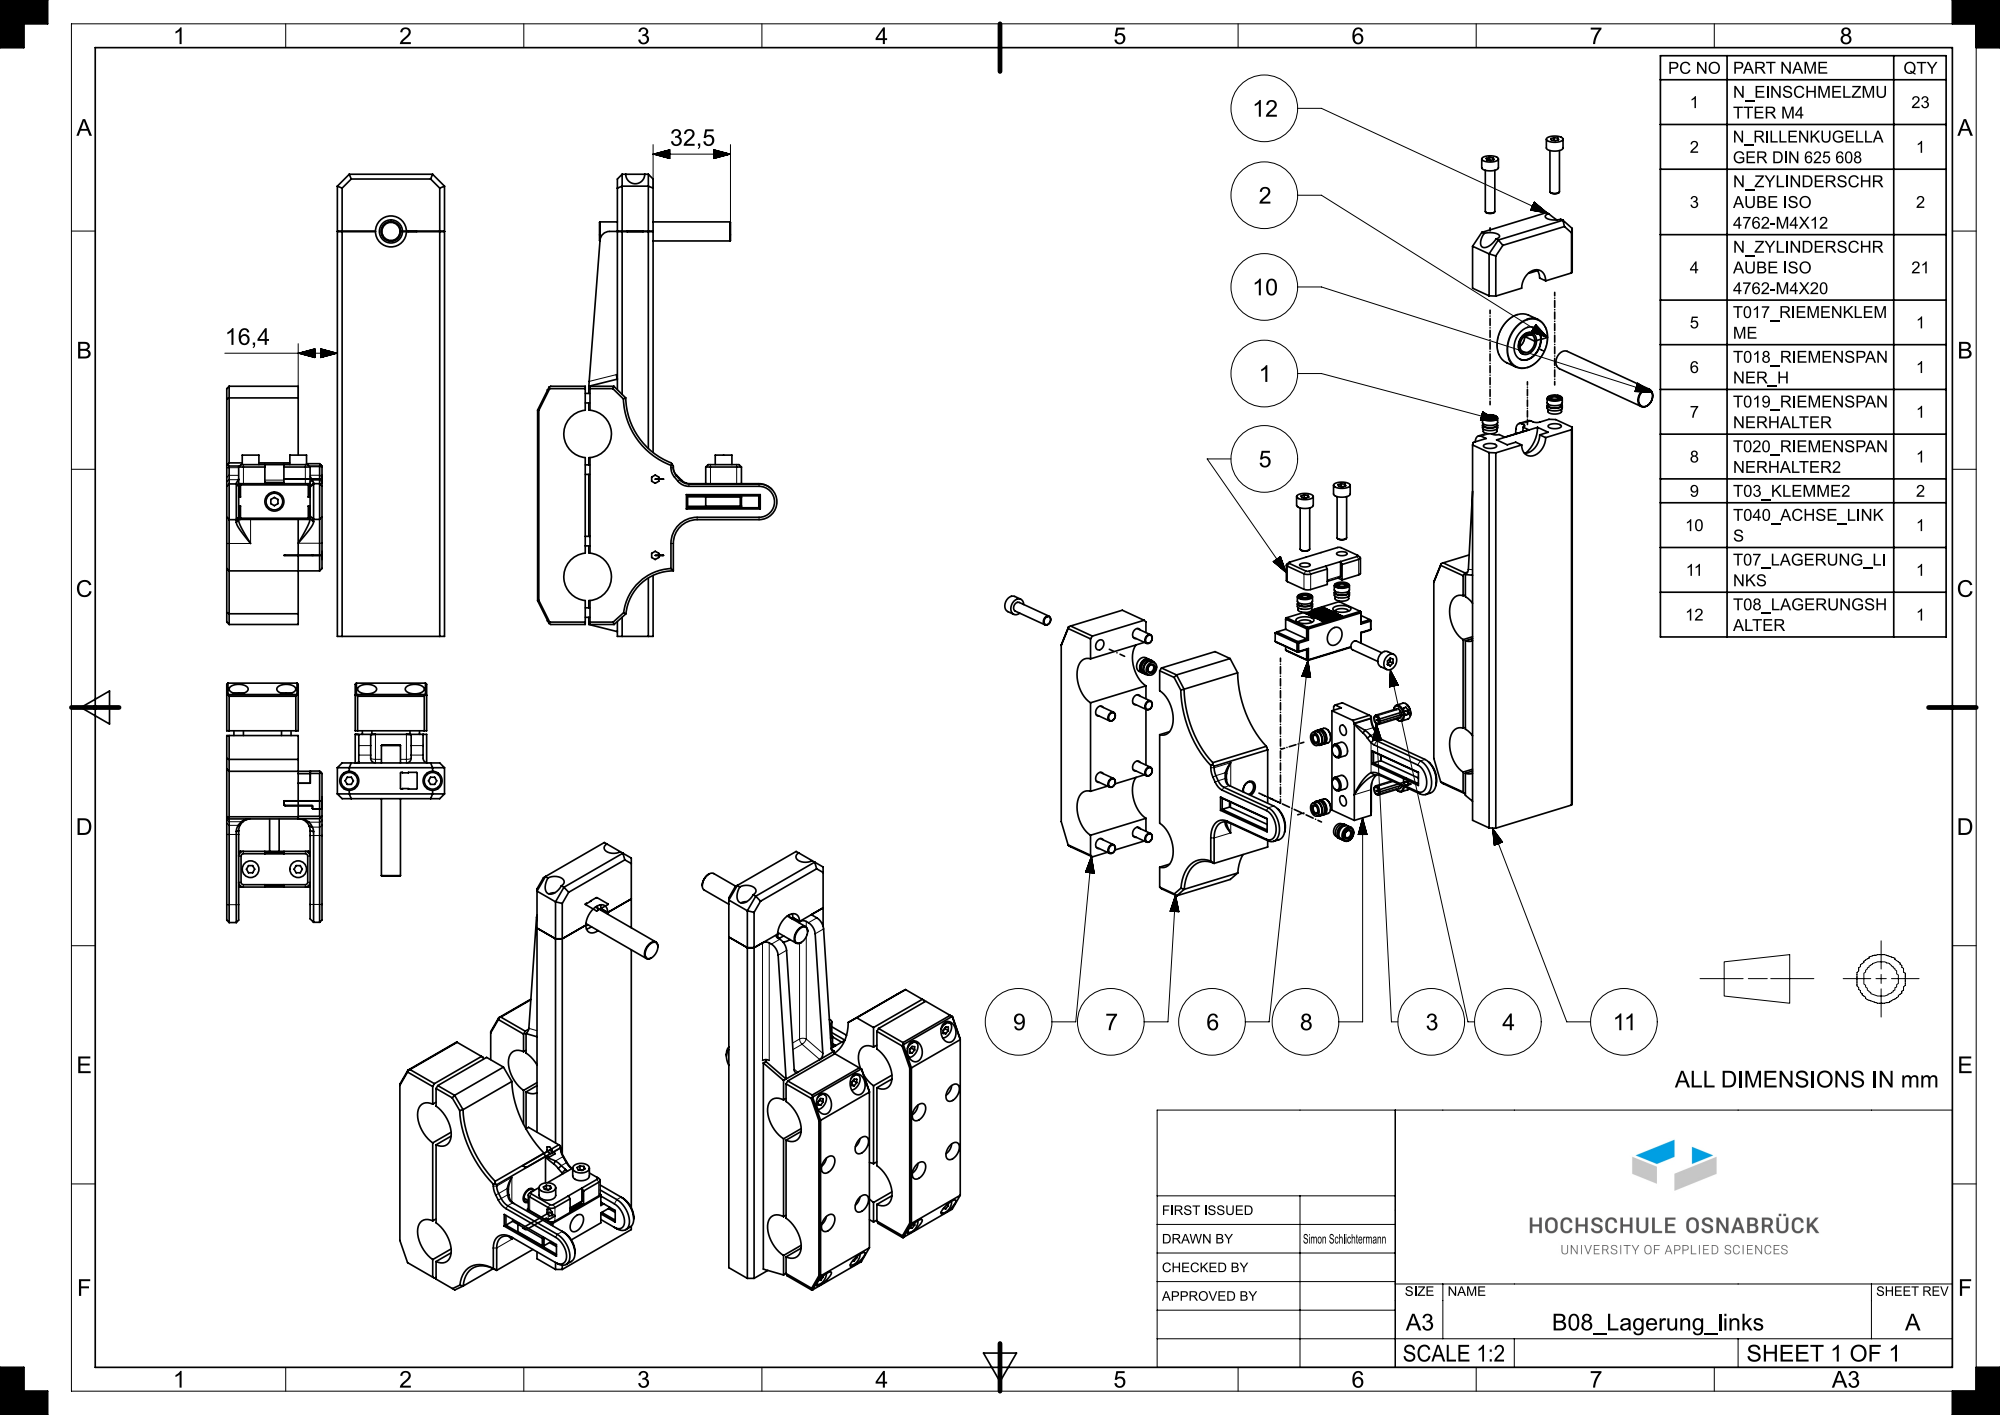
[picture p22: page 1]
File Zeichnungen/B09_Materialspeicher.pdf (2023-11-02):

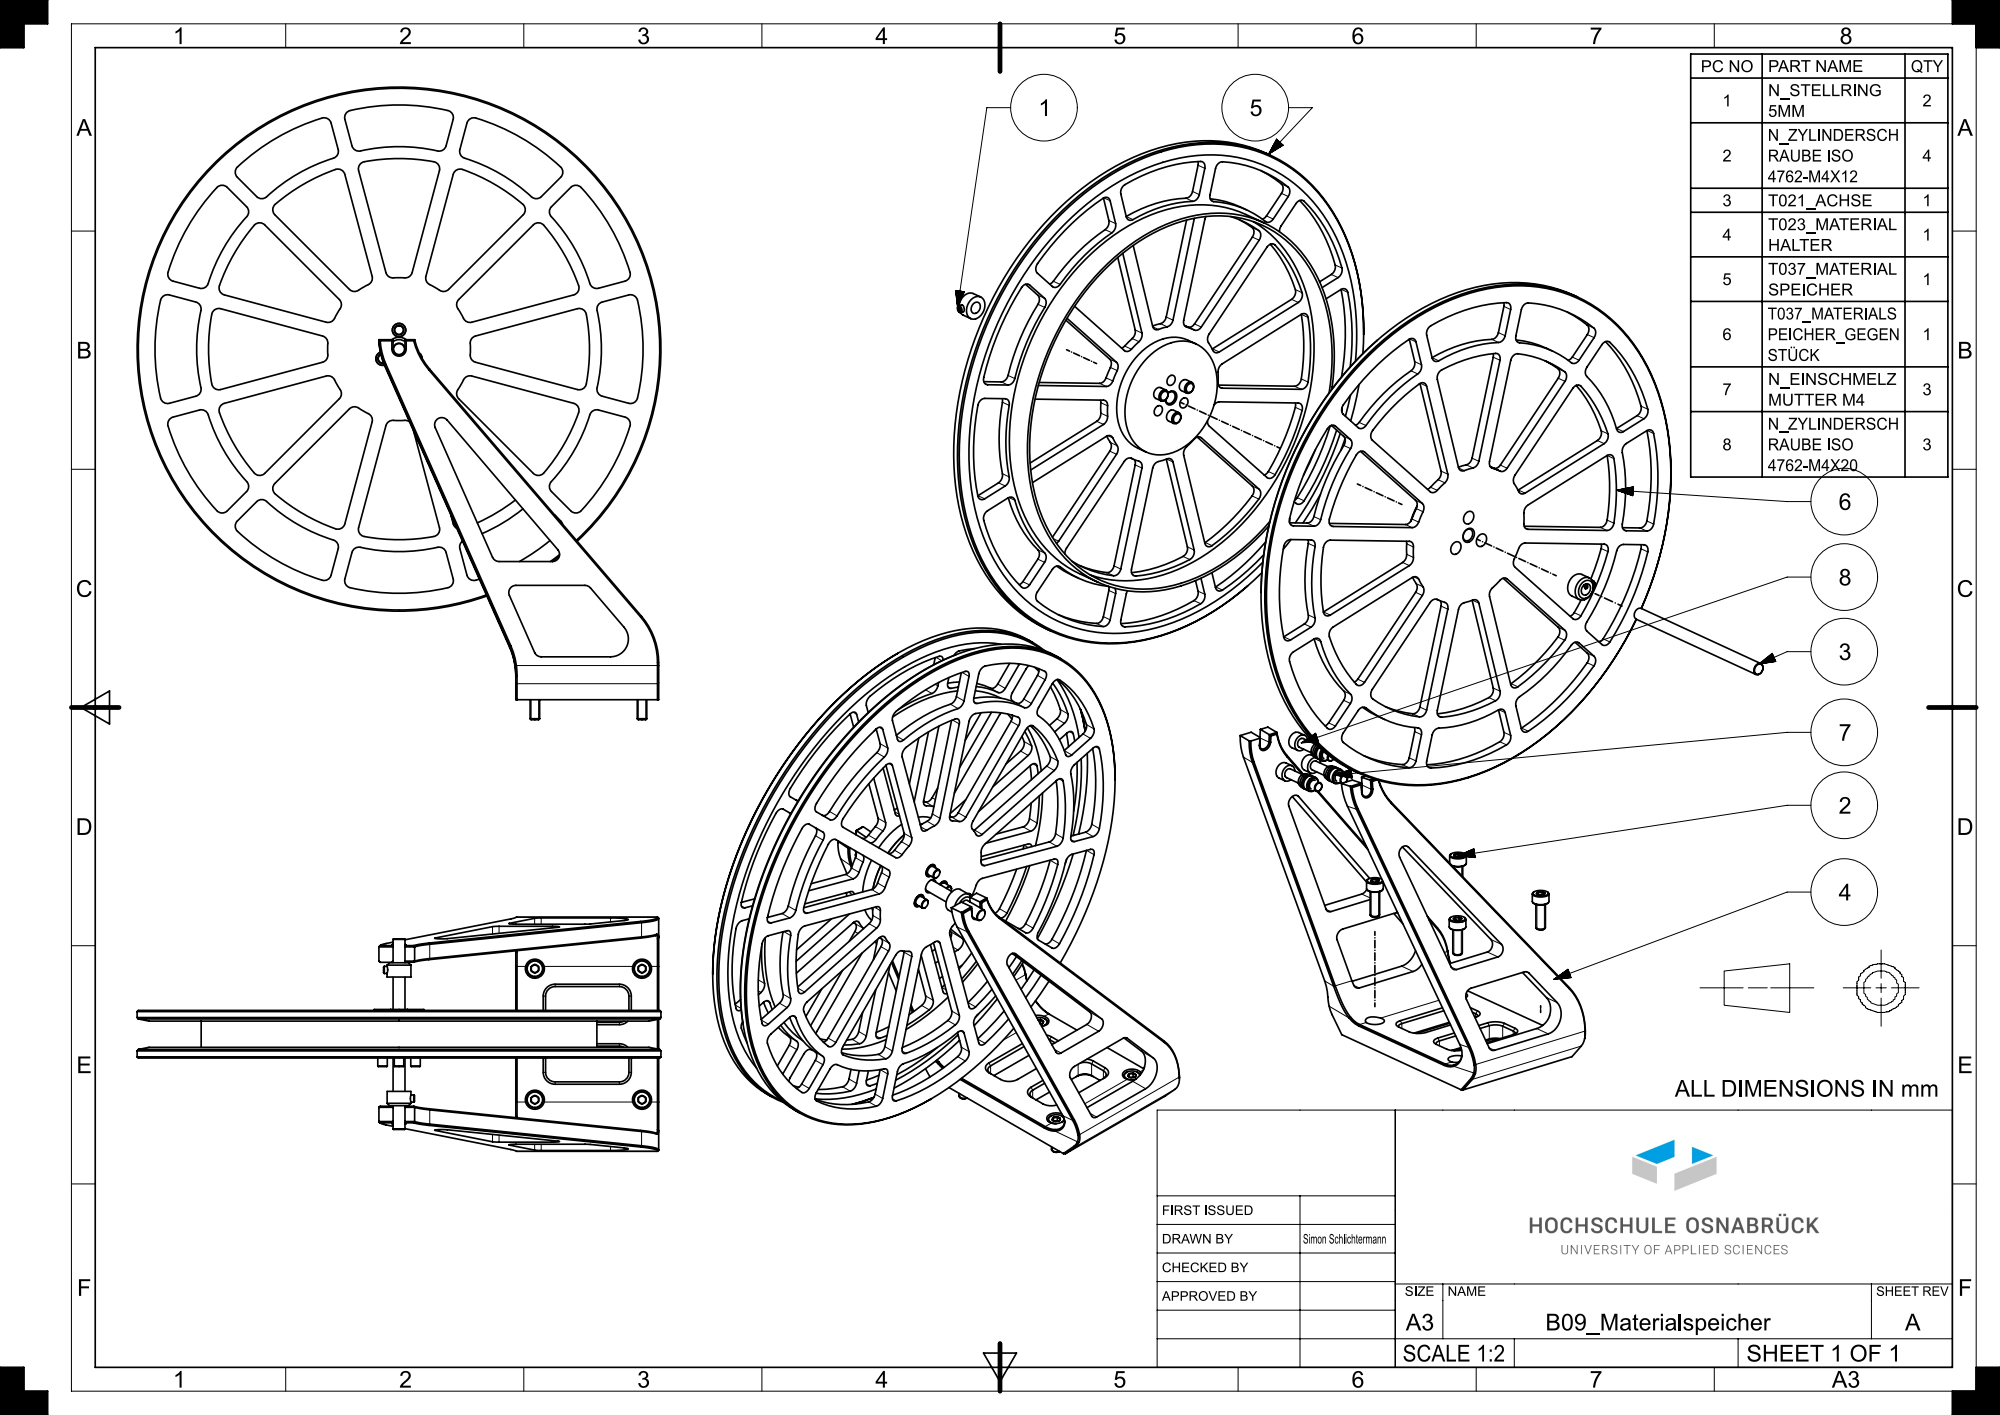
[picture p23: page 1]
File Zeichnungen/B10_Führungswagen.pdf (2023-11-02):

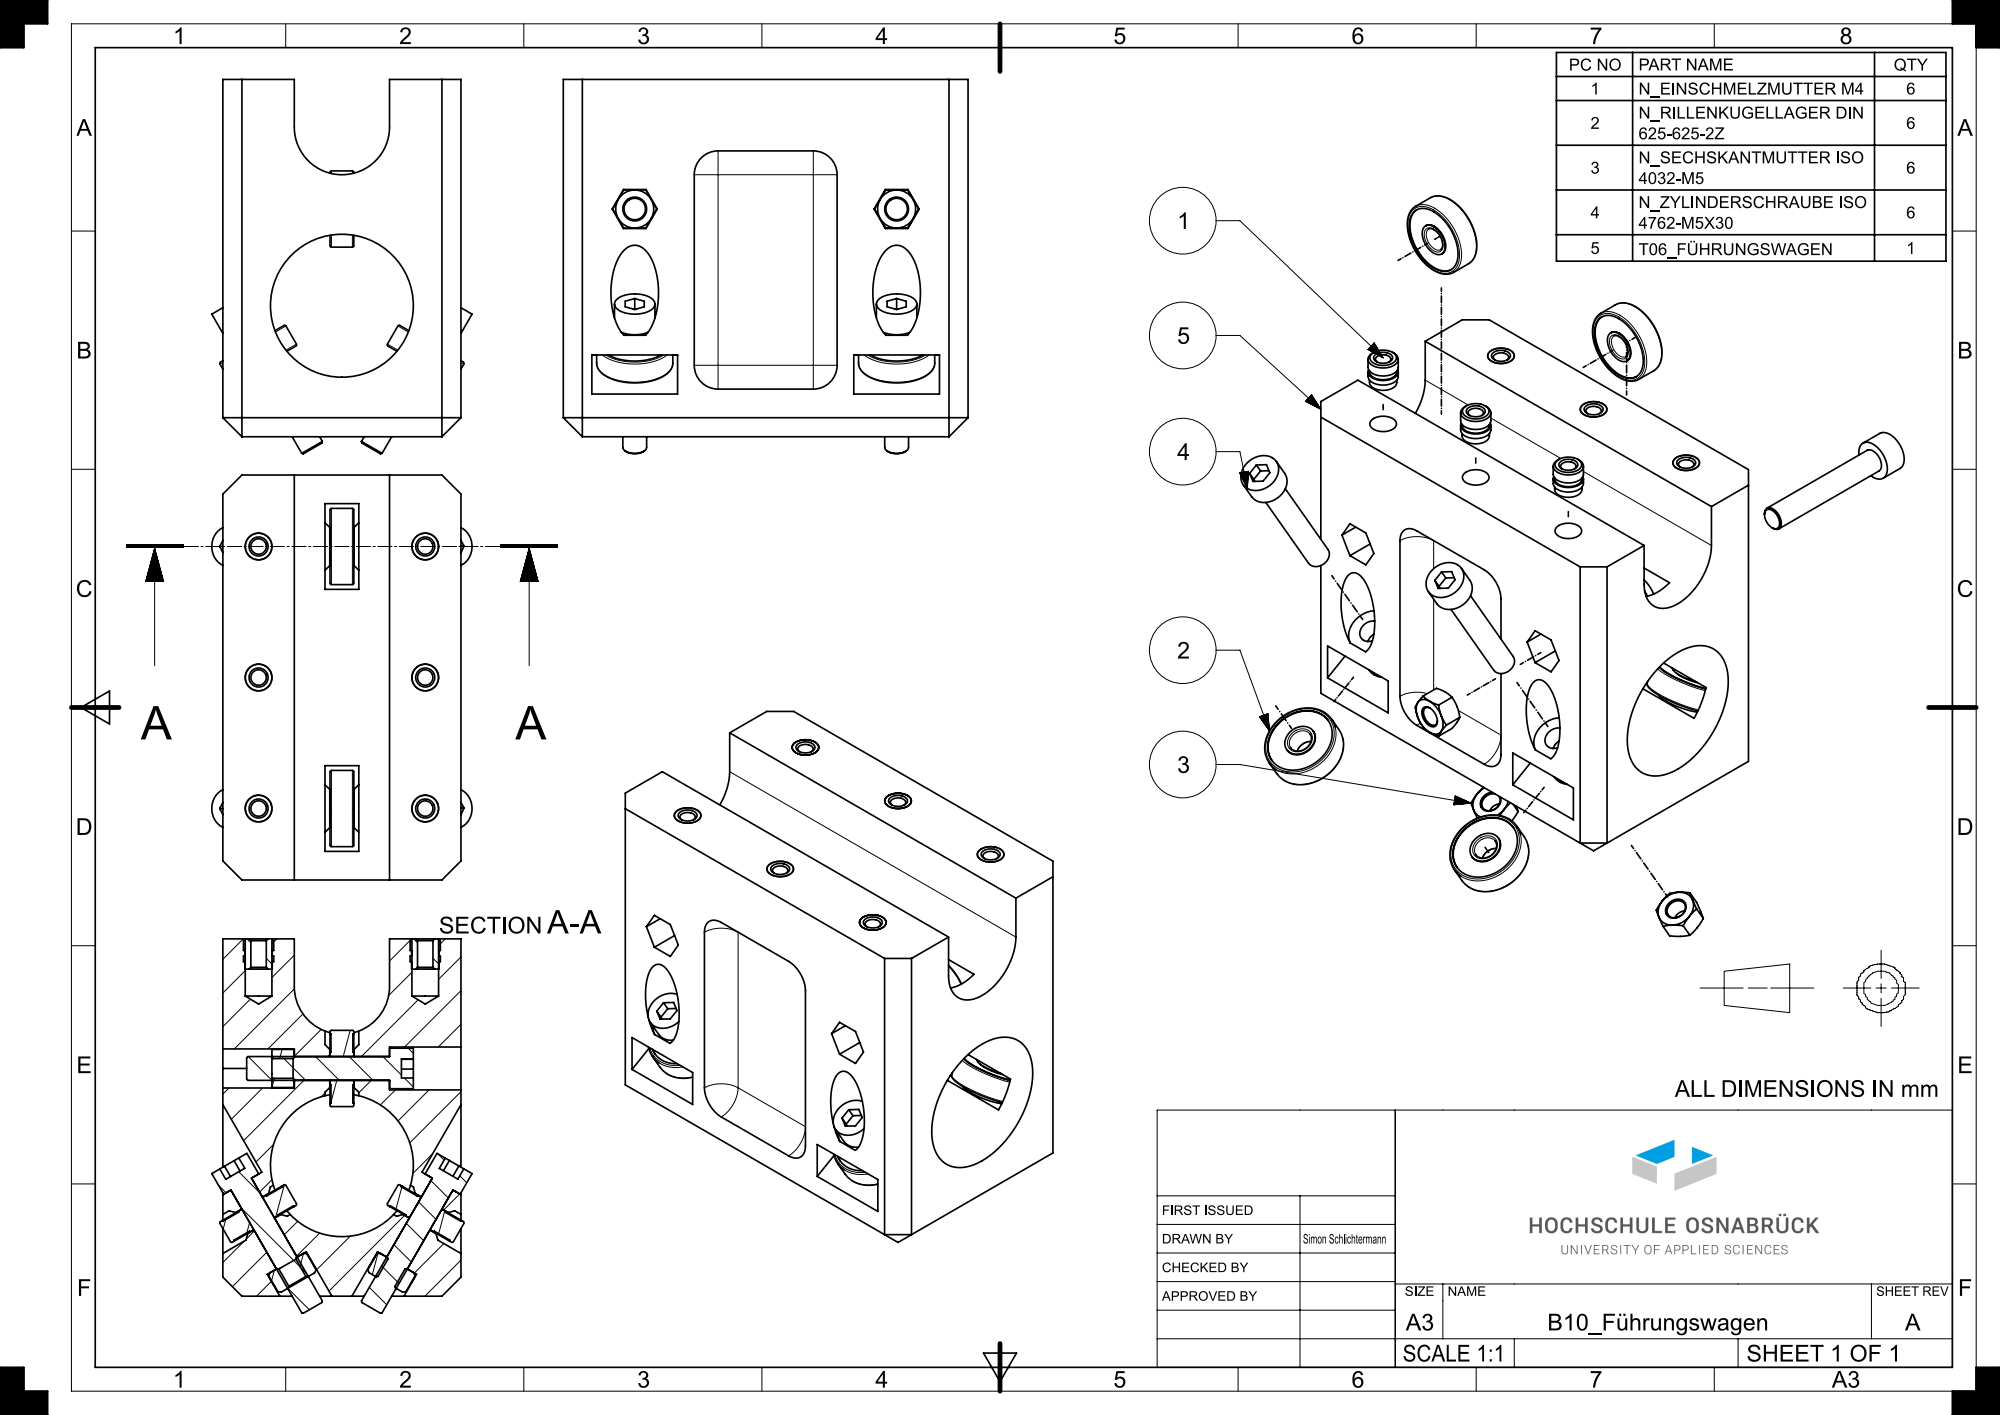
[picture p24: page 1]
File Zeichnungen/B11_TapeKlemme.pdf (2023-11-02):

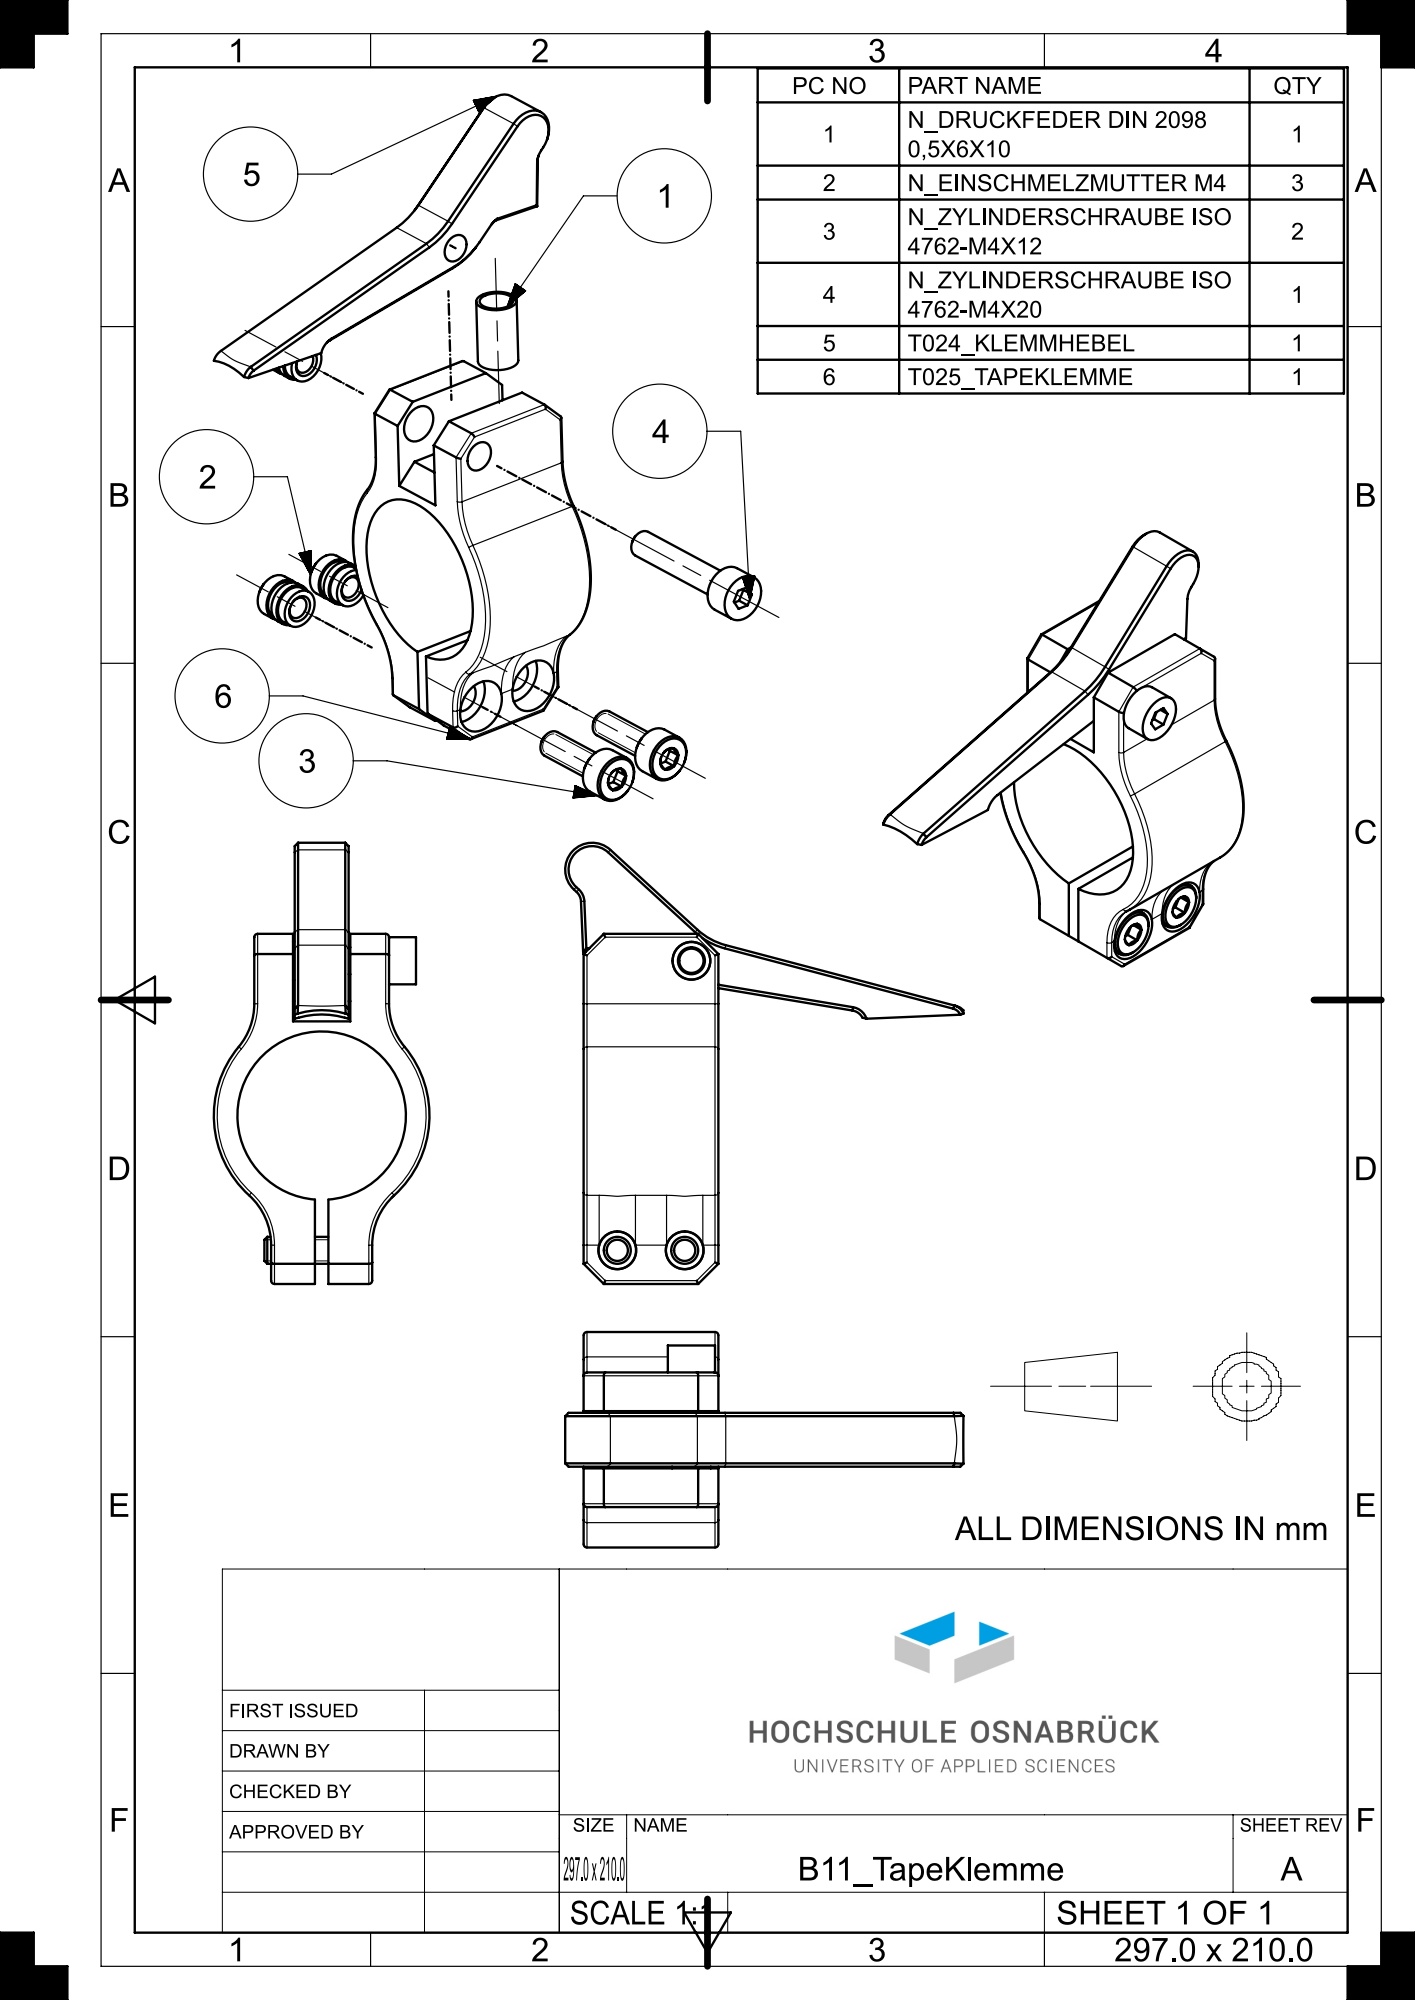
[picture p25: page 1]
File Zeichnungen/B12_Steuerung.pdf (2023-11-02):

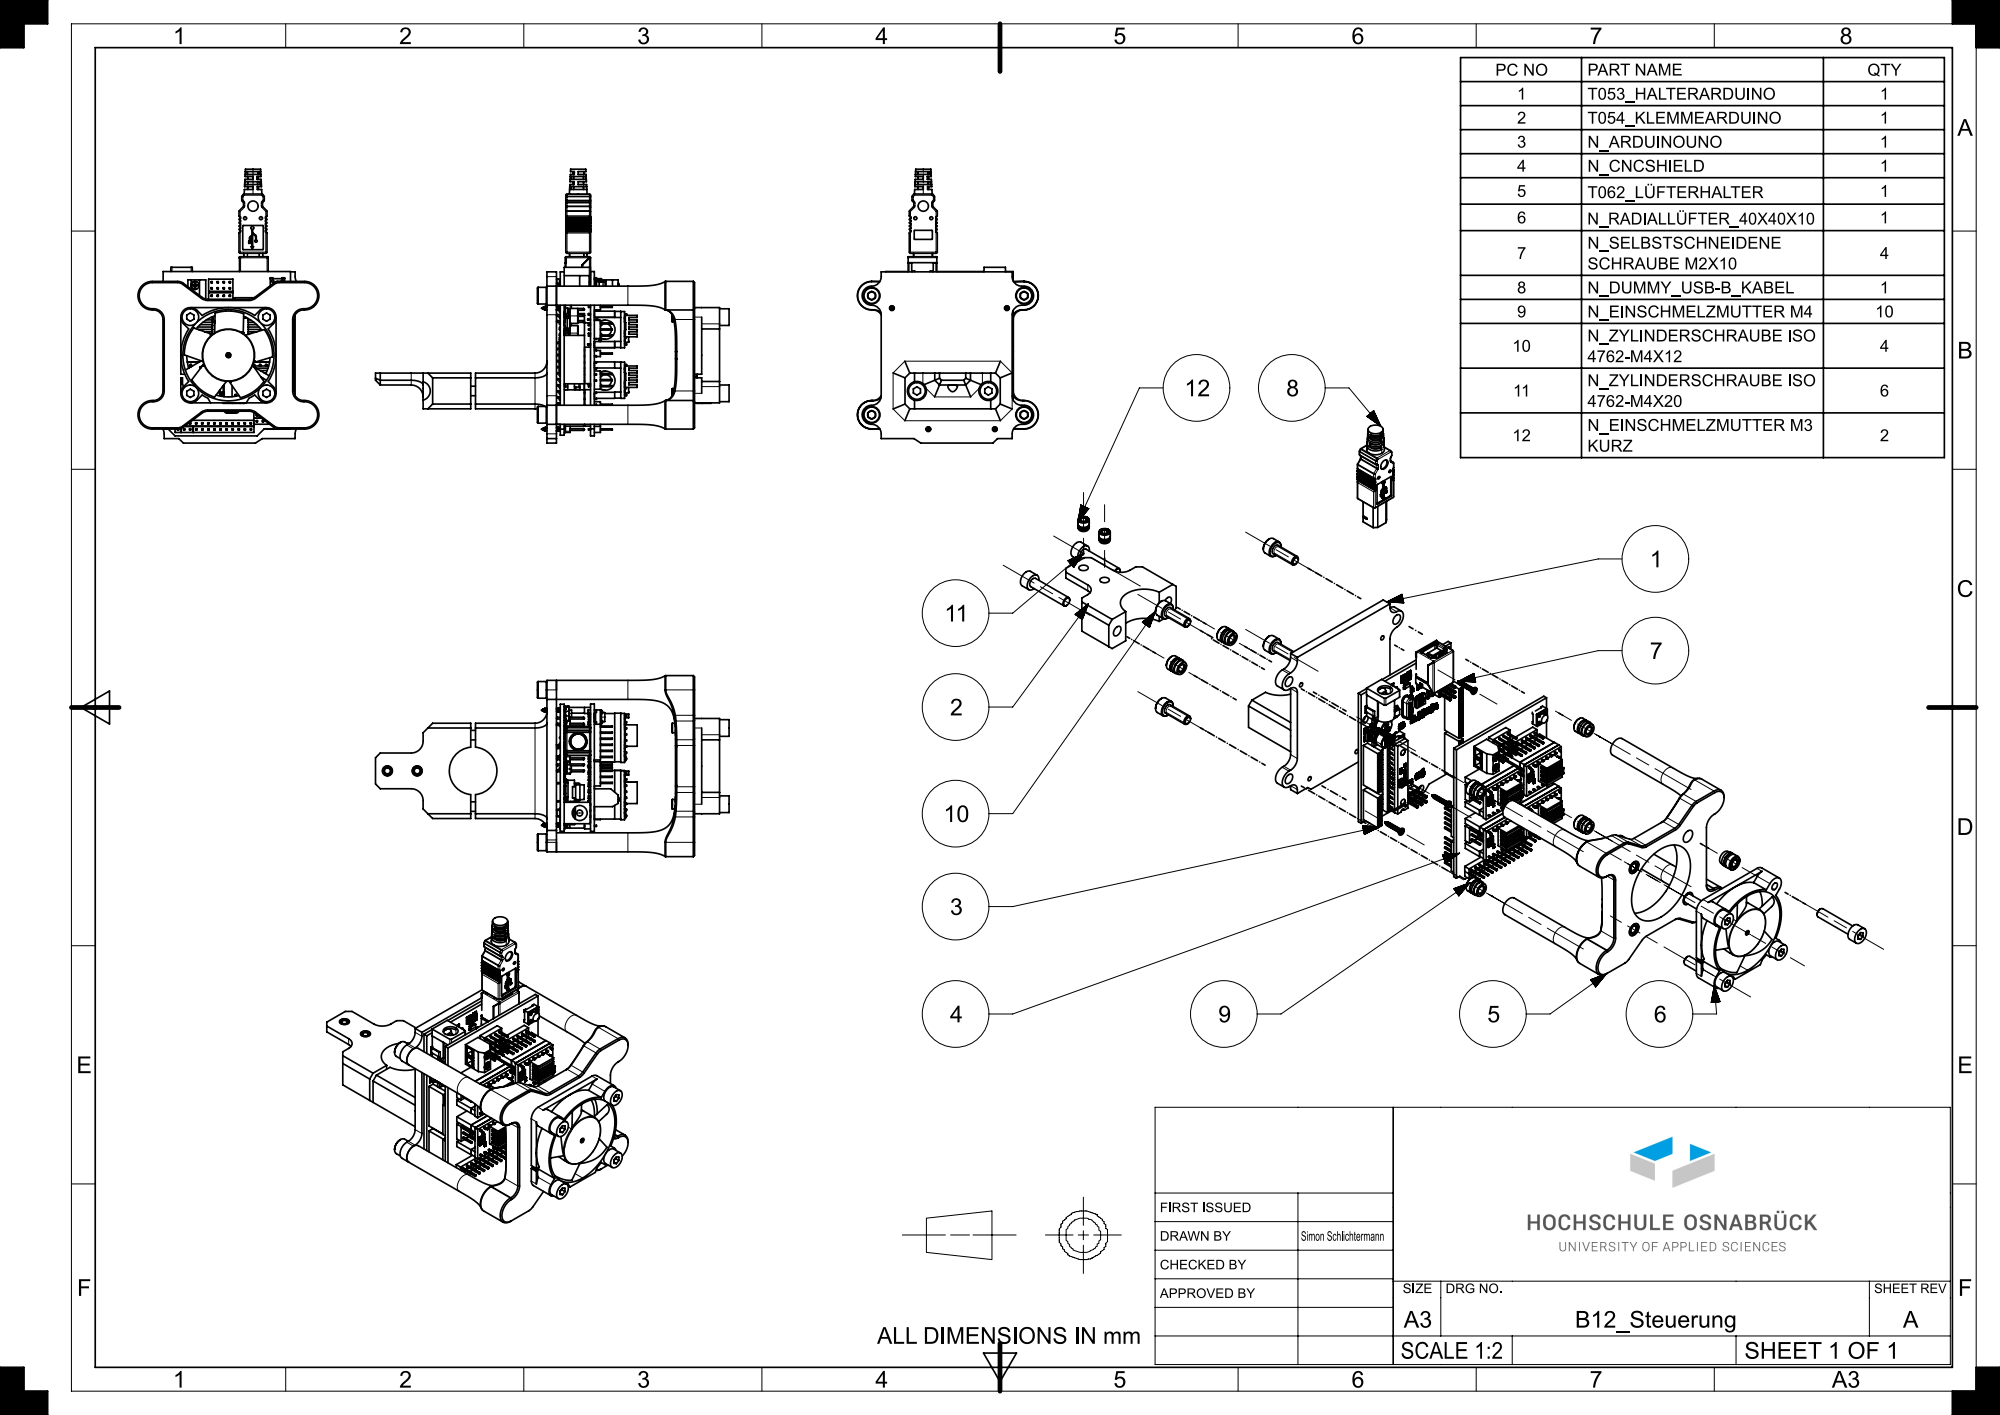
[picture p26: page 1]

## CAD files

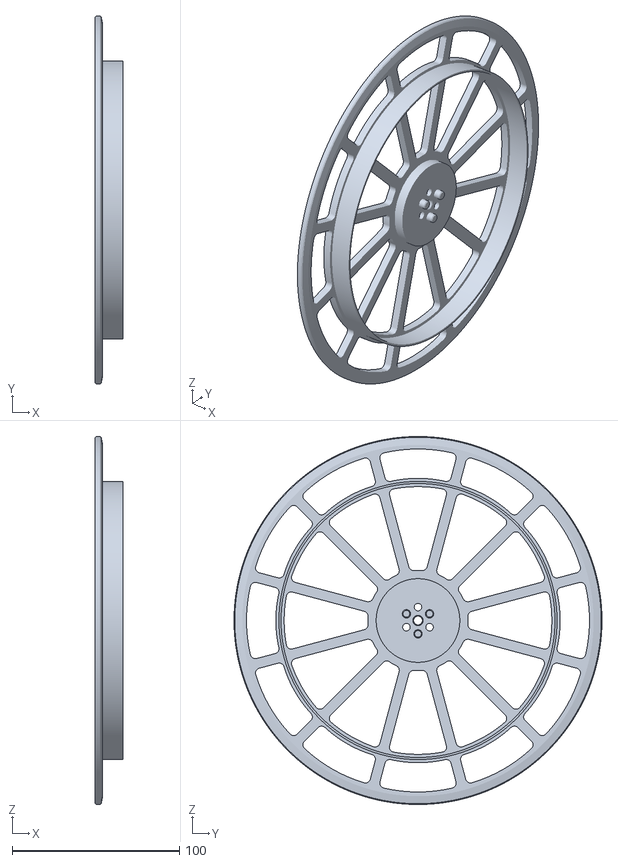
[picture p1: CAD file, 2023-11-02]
Stl/T037_Materialspeicher.stl
16.5 x 220.0 x 220.0

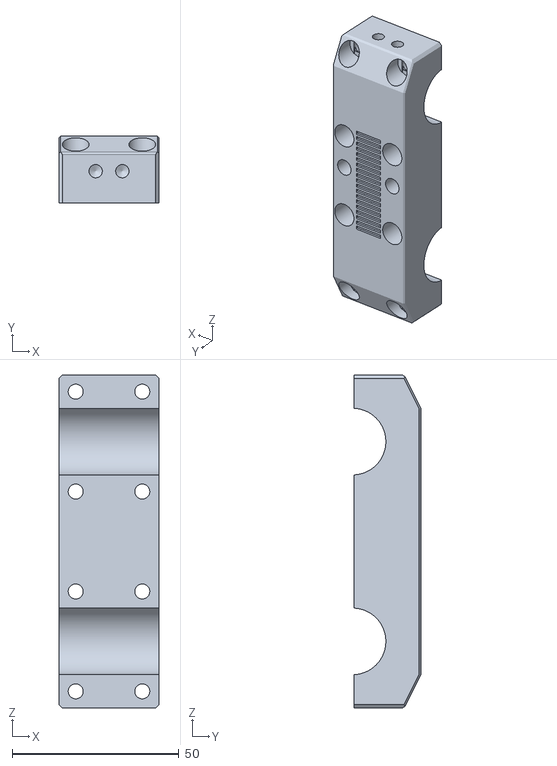
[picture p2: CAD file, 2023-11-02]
Stl/T16_Klemme Riemen.stl
30.0 x 20.0 x 100.0

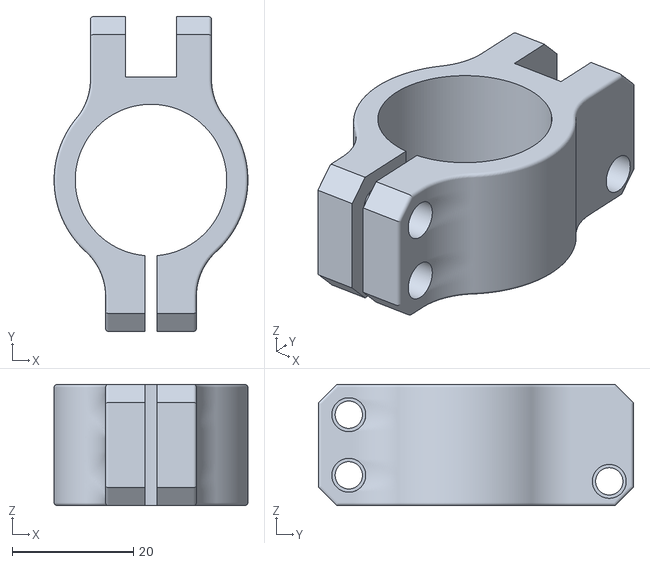
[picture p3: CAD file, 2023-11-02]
Stl/T025_Tapeklemme.stl
32.0 x 52.0 x 20.0

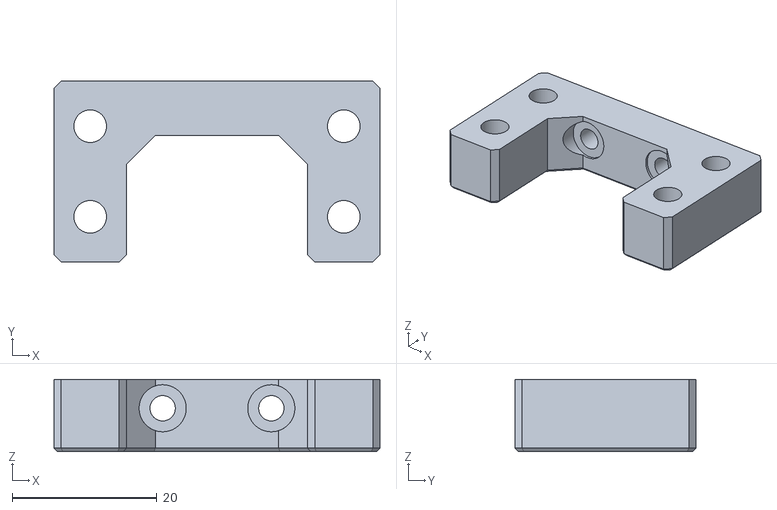
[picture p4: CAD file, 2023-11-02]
Stl/T044_Riemenspannung.stl
45.0 x 25.0 x 10.0

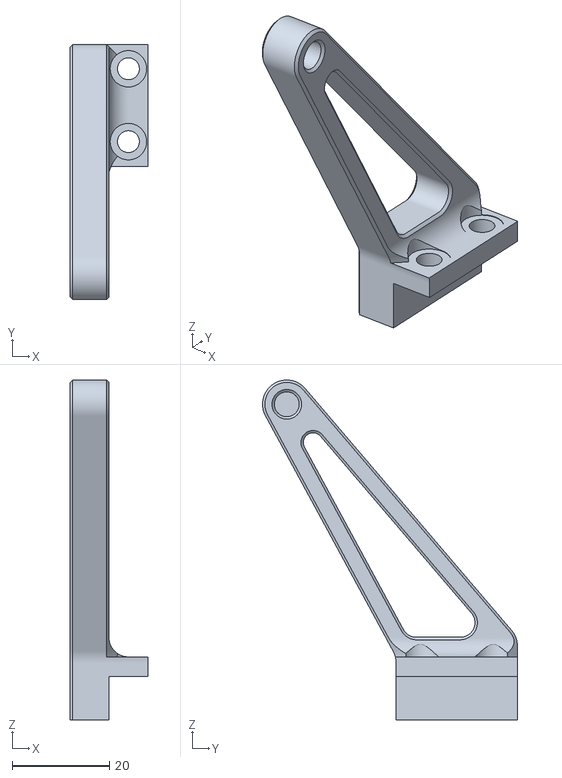
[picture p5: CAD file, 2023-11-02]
Stl/T051_Halter_Umlenkung1gsp.stl
16.0 x 52.5 x 70.0

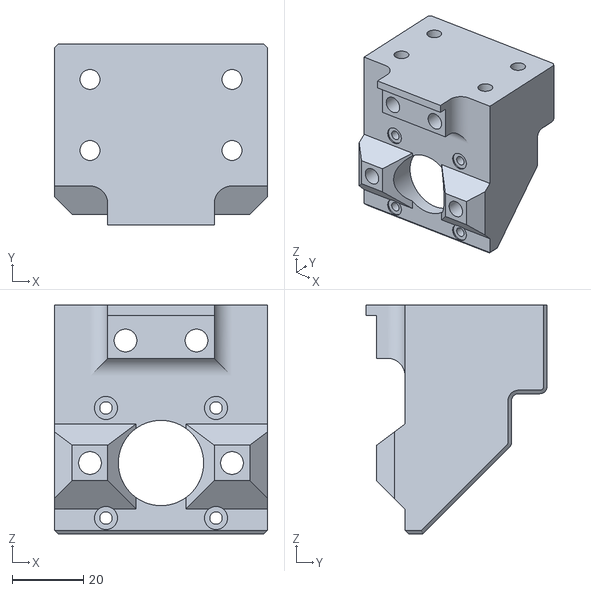
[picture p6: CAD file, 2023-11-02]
Stl/T014_Motorbefestigung2.stl
60.0 x 51.0 x 64.5

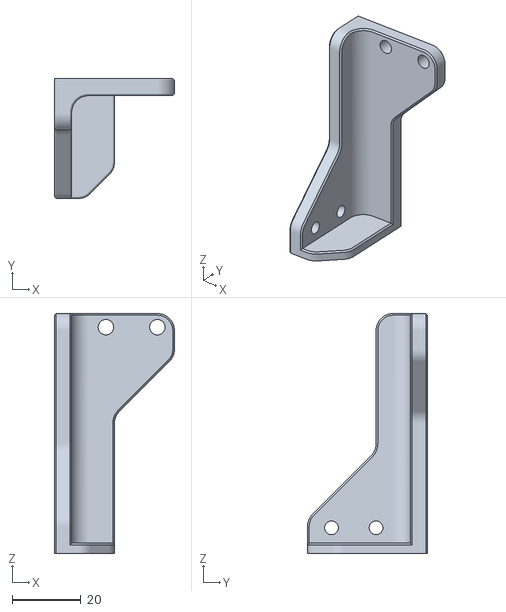
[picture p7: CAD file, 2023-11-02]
Stl/T055_KabelkanalAnschluss.stl
35.0 x 35.0 x 70.0

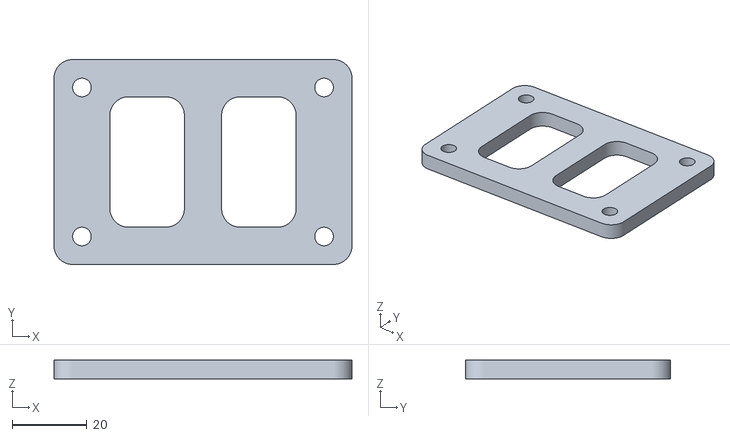
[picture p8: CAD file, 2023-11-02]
Stl/T058_Distanzstück_5mm.stl
80.0 x 55.0 x 5.00

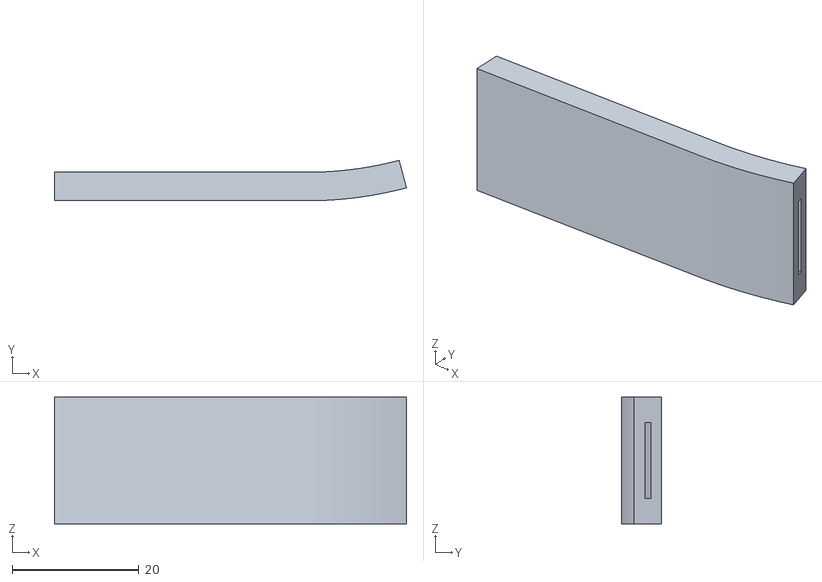
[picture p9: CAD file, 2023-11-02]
Stl/T057_Tapeführung_10mm.stl
55.6 x 6.39 x 20.0

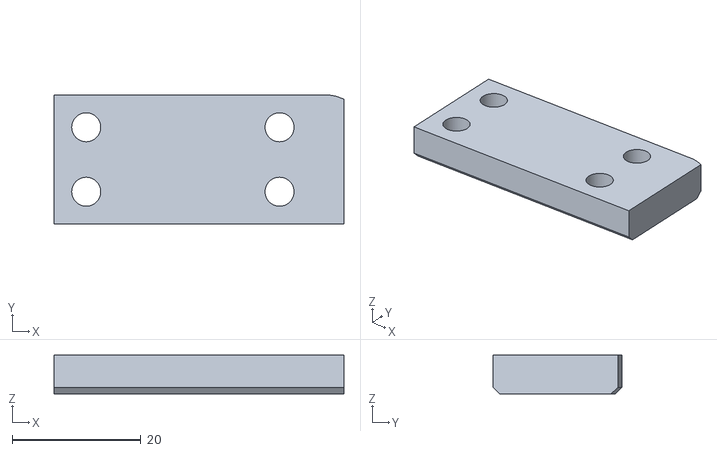
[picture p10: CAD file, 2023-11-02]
Stl/T039_Materialzufuhr_Gegenstück.stl
45.0 x 20.0 x 6.00

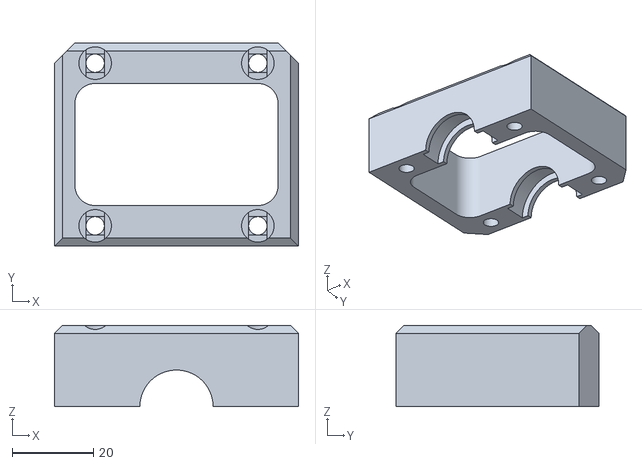
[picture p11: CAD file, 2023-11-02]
Stl/T012_Lagergehäuse.stl
60.0 x 50.0 x 20.0

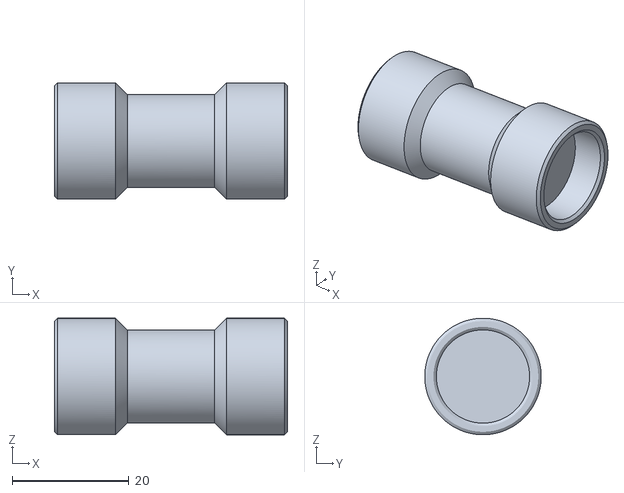
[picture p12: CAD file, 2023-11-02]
Stl/T050_Umlenkrolle.stl
40.0 x 20.0 x 20.0

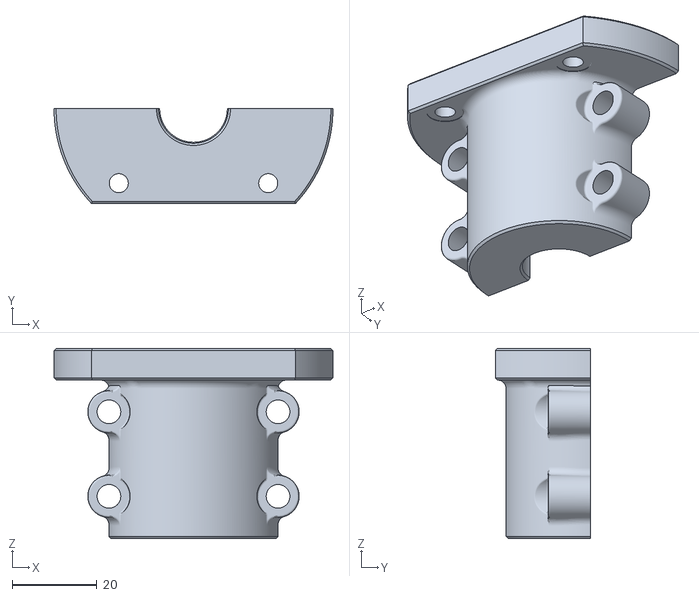
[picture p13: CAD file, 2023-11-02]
Stl/T030_Lager_Gegenstück.stl
66.0 x 22.5 x 45.0

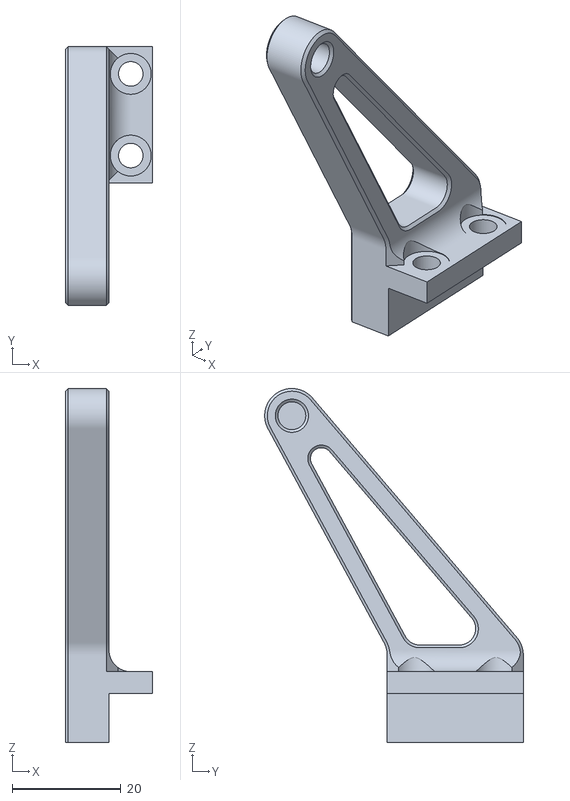
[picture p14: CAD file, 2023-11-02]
Stl/T051_Halter_Umlenkung1gsp_bk.stl
16.0 x 47.5 x 65.0

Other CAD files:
Stl/T051_Halter_Umlenkung1.stl
Stl/T042_Zentrierteil.stl
Stl/T023_Materialhalter.stl
Stl/T056_Abstandshülse.stl
Stl/T010_Motorbefestigung.stl
Stl/T011_Lagergehäuse.stl
Stl/T015_Halter.stl
Stl/T017_Riemenklemme.stl
Stl/T018_Riemenspanner_H.stl
Stl/T019_RiemenspannerHalter.stl
Stl/T01_Standfuß.stl
Stl/T01_Standfuß_gsp.stl
Stl/T020_RiemenspannerHalter2.stl
Stl/T024_Klemmhebel.stl
Stl/T02_Klemme1.stl
Stl/T030_Lager.stl
Stl/T031_Hülse.stl
Stl/T032_Motorbefestigung3.stl
Stl/T033_Federung.stl
Stl/T033_Federung_bk.stl
Stl/T034_Federhalter.stl
Stl/T035_Schieber.stl
Stl/T037_Materialspeicher_Gegenstück.stl
Stl/T039_Materialzufuhr.stl
Stl/T03_Klemme2.stl
Stl/T041_Rohraufnahme_links_21mm.stl
Stl/T043_Rohraufnahme_rechts.stl
Stl/T046_HLHalterO.stl
Stl/T047_Anschlag45°.stl
Stl/T048_Sensorhalter_X.stl
Stl/T048_Sensorhalter_X_Gegenstück.stl
Stl/T049_Spurhalter.stl
Stl/T051_Halter_Umlenkung1_bk.stl
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
